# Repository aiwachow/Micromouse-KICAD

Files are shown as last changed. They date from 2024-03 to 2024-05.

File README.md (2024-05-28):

# Micromouse 2.0 class robot 
Micromouse is a autonomous robot whose purpose is to drive through the maze in the shortest time. 
This design include microcontrollers like STM32 and ESP32. Esp was added to testing over-the-air update  
and wireless communication for STM32. Walls are detecting by IR diodes and phototransistors. 

micromousik

## Used software: 
kicadlogo stm32cubeideLOGO
## Things that have been tested and work:
- [x] Hardware 
- [x] STM32, flashing via ST-LINK  
- [x] Dc motors (with driver)
- [x] Encoders 
- [x] Proximity sensor 
- [ ] ESP32

## Software 

In the future, there will be a description of two approaches to the robot's software, as two two-person teams are working on the project.

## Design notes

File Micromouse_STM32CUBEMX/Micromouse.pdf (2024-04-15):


15/04/2024

## Micromouse Project Configuration Report

# 1. Description

## 1.1. Project

Project Name | Micromouse
Board Name | custom
Generated with: | STM32CubeMX 6.8.1
Date | 04/15/2024

## 1.2. MCU

MCU Series | STM32F4
MCU Line | STM32F405/415
MCU name | STM32F405RGTx
MCU Package | LQFP64
MCU Pin number | 64

## 1.3. Core(s) information

Core(s) | Arm Cortex-M4

# 2. Pinout Configuration

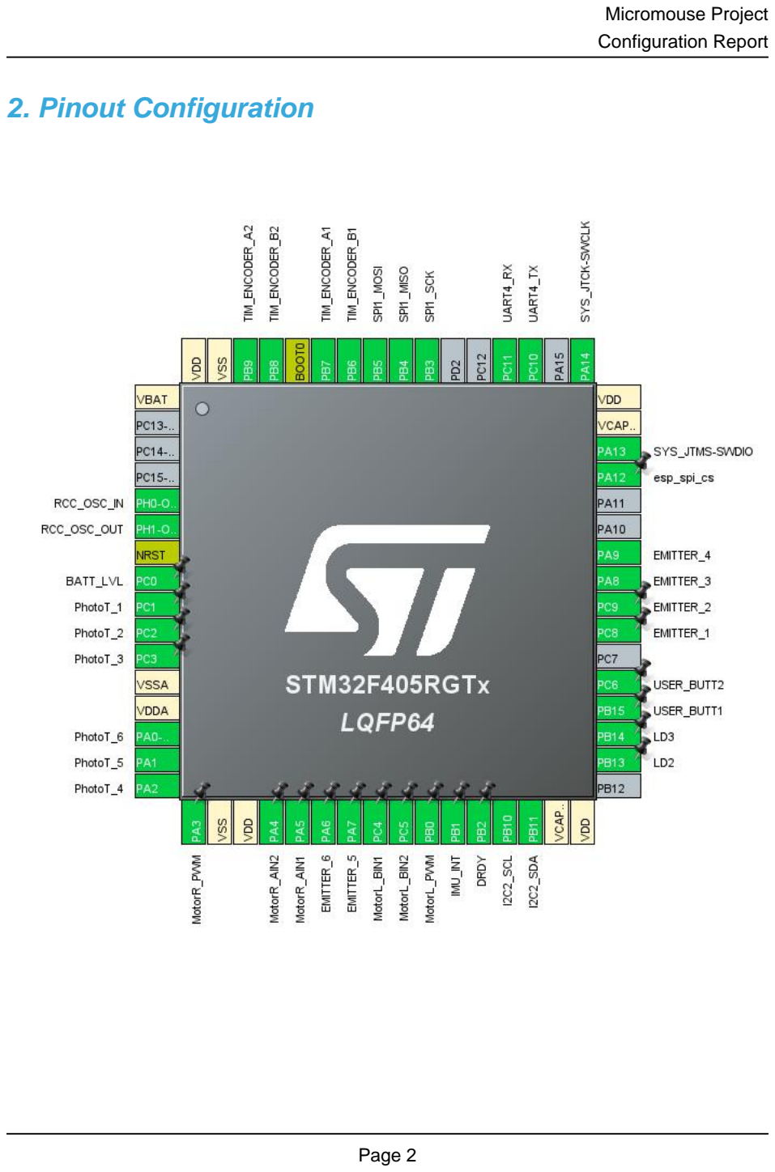
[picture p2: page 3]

# 3. Pins Configuration

Pin Number LQFP64 | Pin Name (function after reset) | Pin Type | Alternate Function(s) | Label
1 | VBAT | Power
5 | PH0-OSC_IN | I/O | RCC_OSC_IN
6 | PH1-OSC_OUT | I/O | RCC_OSC_OUT
7 | NRST | Reset
8 | PC0 | I/O | ADC3_IN10 | BATT_LVL
9 | PC1 | I/O | ADC1_IN11 | PhotoT_1
10 | PC2 | I/O | ADC1_IN12 | PhotoT_2
11 | PC3 | I/O | ADC1_IN13 | PhotoT_3
12 | VSSA | Power
13 | VDDA | Power
14 | PA0-WKUP | I/O | ADC1_IN0 | PhotoT_6
15 | PA1 | I/O | ADC1_IN1 | PhotoT_5
16 | PA2 | I/O | ADC1_IN2 | PhotoT_4
17 | PA3 | I/O | TIM9_CH2 | MotorR_PWM
18 | VSS | Power
19 | VDD | Power
20 | PA4 * | I/O | GPIO_Output | MotorR_AIN2
21 | PA5 * | I/O | GPIO_Output | MotorR_AIN1
22 | PA6 | I/O | TIM3_CH1 | EMITTER_6
23 | PA7 | I/O | TIM3_CH2 | EMITTER_5
24 | PC4 * | I/O | GPIO_Output | MotorL_BIN1
25 | PC5 * | I/O | GPIO_Output | MotorL_BIN2
26 | PB0 | I/O | TIM3_CH3 | MotorL_PWM
27 | PB1 | I/O | GPIO_EXTI1 | IMU_INT
28 | PB2 | I/O | GPIO_EXTI2 | DRDY
29 | PB10 | I/O | I2C2_SCL
30 | PB11 | I/O | I2C2_SDA
31 | VCAP_1 | Power
32 | VDD | Power
34 | PB13 * | I/O | GPIO_Output | LD2
35 | PB14 * | I/O | GPIO_Output | LD3
36 | PB15 | I/O | GPIO_EXTI15 | USER_BUTT1
37 | PC6 | I/O | GPIO_EXTI6 | USER_BUTT2
39 | PC8 | I/O | TIM8_CH3 | EMITTER_1
40 | PC9 | I/O | TIM3_CH4 | EMITTER_2
41 | PA8 | I/O | TIM1_CH1 | EMITTER_3

Pin Number LQFP64 | Pin Name (function after reset) | Pin Type | Alternate Function(s) | Label
42 | PA9 | I/O | TIM1_CH2 | EMITTER_4
45 | PA12 * | I/O | GPIO_Output | esp_spi_cs
46 | PA13 | I/O | SYS_JTMS-SWDIO
47 | VCAP_2 | Power
48 | VDD | Power
49 | PA14 | I/O | SYS_JTCK-SWCLK
51 | PC10 | I/O | UART4_TX
52 | PC11 | I/O | UART4_RX
55 | PB3 | I/O | SPI1_SCK
56 | PB4 | I/O | SPI1_MISO
57 | PB5 | I/O | SPI1_MOSI
58 | PB6 | I/O | TIM4_CH1 | TIM_ENCODER_B1
59 | PB7 | I/O | TIM4_CH2 | TIM_ENCODER_A1
60 | BOOT0 | Boot
61 | PB8 | I/O | TIM4_CH3 | TIM_ENCODER_B2
62 | PB9 | I/O | TIM4_CH4 | TIM_ENCODER_A2
63 | VSS | Power
64 | VDD | Power

## * The pin is affected with an I/O function

# 4. Clock Tree Configuration

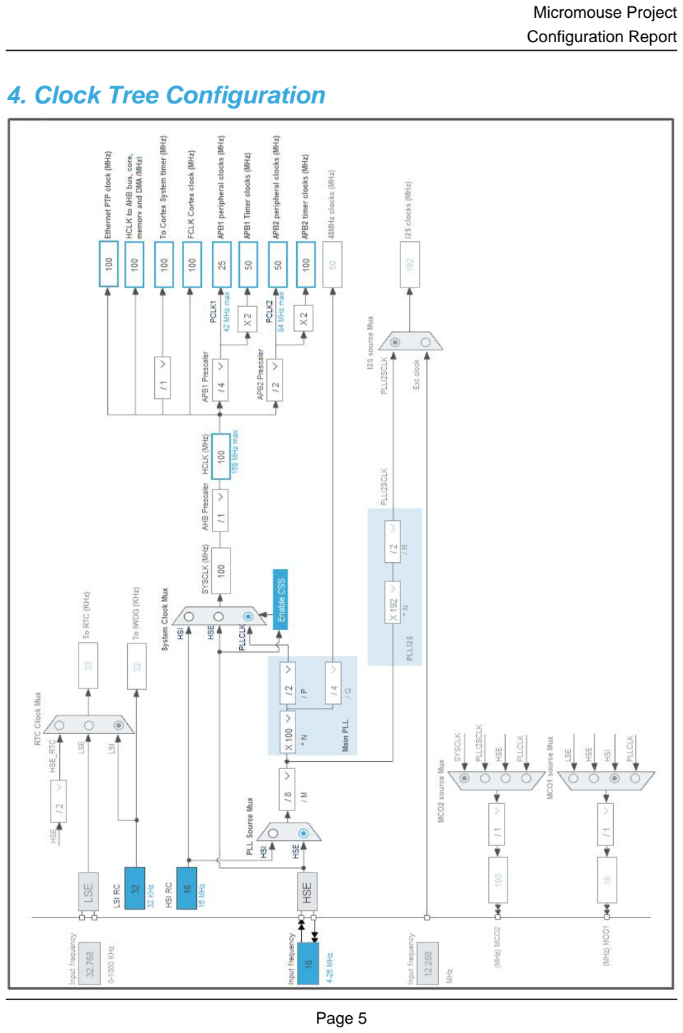
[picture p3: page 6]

# 5. Software Project

## 5.1. Project Settings

Name | Value
Project Name | Micromouse
Project Folder | D:\Micromouse\Micromouse_Kicad\Micromouse_STM32CUBEMX
Toolchain / IDE | STM32CubeIDE
Firmware Package Name and Version | STM32Cube FW_F4 V1.27.1
Application Structure | Advanced
Generate Under Root | Yes
Do not generate the main() | No
Minimum Heap Size | 0x200
Minimum Stack Size | 0x400

## 5.2. Code Generation Settings

Name | Value
STM32Cube MCU packages and embedded software | Copy only the necessary library files
Generate peripheral initialization as a pair of '.c/.h' files | No
Backup previously generated files when re-generating | No
Keep User Code when re-generating | Yes
Delete previously generated files when not re-generated | Yes
Set all free pins as analog (to optimize the power consumption) | No
Enable Full Assert | No

## 5.3. Advanced Settings - Generated Function Calls

Rank | Function Name | Peripheral Instance Name
1 | SystemClock_Config | RCC
2 | MX_GPIO_Init | GPIO
3 | MX_DMA_Init | DMA
4 | MX_ADC1_Init | ADC1
5 | MX_SPI1_Init | SPI1
6 | MX_TIM1_Init | TIM1
7 | MX_TIM3_Init | TIM3
8 | MX_TIM4_Init | TIM4
9 | MX_UART4_Init | UART4
10 | MX_I2C2_Init | I2C2
11 | MX_TIM8_Init | TIM8

Rank | Function Name | Peripheral Instance Name
12 | MX_TIM9_Init | TIM9
13 | MX_ADC3_Init | ADC3

# 6. Power Consumption Calculator report

## 6.1. Microcontroller Selection

Series | STM32F4
Line | STM32F405/415
MCU | STM32F405RGTx
Datasheet | DS8626_Rev8

## 6.2. Parameter Selection

Temperature | 25
Vdd | 3.3

## 6.3. Battery Selection

Battery | Li-SOCL2(A3400)
Capacity | 3400.0 mAh
Self Discharge | 0.08 %/month
Nominal Voltage | 3.6 V
Max Cont Current | 100.0 mA
Max Pulse Current | 200.0 mA
Cells in series | 1
Cells in parallel | 1

## 6.4. Sequence

Step | Step1 | Step2
Mode | RUN | STOP
Vdd | 3.3 | 3.3
Voltage Source | Battery | Battery
Range | Scale1-High | No Scale
Fetch Type | FLASH | n/a
CPU Frequency | 168 MHz | 0 Hz
Clock Configuration | HSE PLL | Regulator_LP Flash-PwrDwn
Clock Source Frequency | 4 MHz | 0 Hz

### Peripherals

Additional Cons. | 0 mA | 0 mA
Average Current | 46 mA | 280 µA
Duration | 0.1 ms | 0.9 ms
DMIPS | 210.0 | 0.0
Ta Max | 98.02 | 104.96
Category | In DS Table | In DS Table

## 6.5. Results

Sequence Time | 1 ms | Average Current | 4.85 mA
Battery Life | 29 days, 4 hours | Average DMIPS | 210.0 DMIPS

## 6.6. Chart

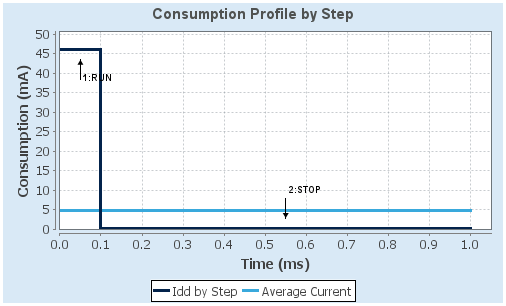
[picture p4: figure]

# 7. Peripherals and Middlewares Configuration

## 7.1. ADC1 mode: IN0 mode: IN1 mode: IN2 mode: IN11 mode: IN12 mode: IN13

## 7.1.1. Parameter Settings:

### ADCs_Common_Settings:

Mode | Independent mode

### ADC_Settings:

Clock Prescaler | PCLK2 divided by 4 *
Resolution | 12 bits (15 ADC Clock cycles)
Data Alignment | Right alignment
Scan Conversion Mode | Enabled
Continuous Conversion Mode | Enabled *
Discontinuous Conversion Mode | Disabled
DMA Continuous Requests | Enabled *
End Of Conversion Selection | EOC flag at the end of single channel conversion

### ADC_Regular_ConversionMode:

Number Of Conversion | 6 *
External Trigger Conversion Source | Regular Conversion launched by software
External Trigger Conversion Edge | None
Rank | 1
Channel | Channel 11 *
Sampling Time | 480 Cycles *
Rank | 2 *
Channel | Channel 12 *
Sampling Time | 480 Cycles *
Rank | 3 *
Channel | Channel 13 *
Sampling Time | 480 Cycles *
Rank | 4 *
Channel | Channel 2 *
Sampling Time | 480 Cycles *

Rank | 5 *
Channel | Channel 1 *
Sampling Time | 480 Cycles *
Rank | 6 *
Channel | Channel 0
Sampling Time | 480 Cycles *

### ADC_Injected_ConversionMode:

Number Of Conversions | 0

### WatchDog:

Enable Analog WatchDog Mode | false

## 7.2. ADC3 mode: IN10

## 7.2.1. Parameter Settings:

### ADC_Settings:

Clock Prescaler | PCLK2 divided by 4 *
Resolution | 12 bits (15 ADC Clock cycles)
Data Alignment | Right alignment
Scan Conversion Mode | Disabled
Continuous Conversion Mode | Enabled *
Discontinuous Conversion Mode | Disabled
DMA Continuous Requests | Disabled
End Of Conversion Selection | EOC flag at the end of single channel conversion

### ADC_Regular_ConversionMode:

Number Of Conversion | 1
External Trigger Conversion Source | Regular Conversion launched by software
External Trigger Conversion Edge | None
Rank | 1
Channel | Channel 10
Sampling Time | 480 Cycles *

### ADC_Injected_ConversionMode:

Number Of Conversions | 0

### WatchDog:

Enable Analog WatchDog Mode | false

## 7.3. I2C2 I2C: I2C

## 7.3.1. Parameter Settings:

### Master Features:

I2C Speed Mode | Fast Mode *
I2C Clock Speed (Hz) | 400000
Fast Mode Duty Cycle | Duty cycle Tlow/Thigh = 2

### Slave Features:

Clock No Stretch Mode | Disabled
Primary Address Length selection | 7-bit
Dual Address Acknowledged | Disabled
Primary slave address | 0
General Call address detection | Disabled

## 7.4. RCC High Speed Clock (HSE): Crystal/Ceramic Resonator

## 7.4.1. Parameter Settings:

### System Parameters:

VDD voltage (V) | 3.3
Instruction Cache | Enabled
Prefetch Buffer | Enabled
Data Cache | Enabled
Flash Latency(WS) | 3 WS (4 CPU cycle)

### RCC Parameters:

HSI Calibration Value | 16
HSE Startup Timout Value (ms) | 100
LSE Startup Timout Value (ms) | 5000

### Power Parameters:

Power Regulator Voltage Scale | Power Regulator Voltage Scale 1

## 7.5. SPI1 Mode: Full-Duplex Master

## 7.5.1. Parameter Settings:

### Basic Parameters:

Frame Format | Motorola
Data Size | 8 Bits
First Bit | MSB First

### Clock Parameters:

Prescaler (for Baud Rate) | 8 *
Baud Rate | 6.25 MBits/s *
Clock Polarity (CPOL) | Low
Clock Phase (CPHA) | 1 Edge

### Advanced Parameters:

CRC Calculation | Disabled
NSS Signal Type | Software

## 7.6. SYS Debug: Serial Wire

## 7.7. TIM1 Clock Source : Internal Clock Channel1: PWM Generation CH1 Channel2: PWM Generation CH2

## 7.7.1. Parameter Settings:

### Counter Settings:

Prescaler (PSC - 16 bits value) | 19 *
Counter Mode | Up
Counter Period (AutoReload Register - 16 bits value ) | 99 *
Internal Clock Division (CKD) | No Division
Repetition Counter (RCR - 8 bits value) | 0
auto-reload preload | Disable

### Trigger Output (TRGO) Parameters:

Master/Slave Mode (MSM bit) | Disable (Trigger input effect not delayed)
Trigger Event Selection | Reset (UG bit from TIMx_EGR)

### Break And Dead Time management - BRK Configuration:

BRK State | Disable
BRK Polarity | High

### Break And Dead Time management - Output Configuration:

Automatic Output State | Disable
Off State Selection for Run Mode (OSSR) | Disable
Off State Selection for Idle Mode (OSSI) | Disable
Lock Configuration | Off

### PWM Generation Channel 1:

Mode | PWM mode 1
Pulse (16 bits value) | 0
Output compare preload | Enable
Fast Mode | Disable
CH Polarity | High
CH Idle State | Reset

### PWM Generation Channel 2:

Mode | PWM mode 1
Pulse (16 bits value) | 0
Output compare preload | Enable
Fast Mode | Disable
CH Polarity | High
CH Idle State | Reset

## 7.8. TIM3 Clock Source : Internal Clock Channel1: PWM Generation CH1 Channel2: PWM Generation CH2 Channel3: PWM Generation CH3 Channel4: PWM Generation CH4

## 7.8.1. Parameter Settings:

### Counter Settings:

Prescaler (PSC - 16 bits value) | 9 *
Counter Mode | Up
Counter Period (AutoReload Register - 16 bits value ) | 99 *
Internal Clock Division (CKD) | No Division
auto-reload preload | Disable

### Trigger Output (TRGO) Parameters:

Master/Slave Mode (MSM bit) | Disable (Trigger input effect not delayed)
Trigger Event Selection | Reset (UG bit from TIMx_EGR)

### PWM Generation Channel 1:

Mode | PWM mode 1
Pulse (16 bits value) | 0
Output compare preload | Enable
Fast Mode | Disable
CH Polarity | High

### PWM Generation Channel 2:

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

### PWM Generation Channel 3:

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

### PWM Generation Channel 4:

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

## 7.9. TIM4 Channel1: Input Capture direct mode Channel2: Input Capture direct mode Channel3: Input Capture direct mode Channel4: Input Capture direct mode

## 7.9.1. Parameter Settings:

### Counter Settings:

Prescaler (PSC - 16 bits value) | 0
Counter Mode | Up
Counter Period (AutoReload Register - 16 bits value ) | 65535
Internal Clock Division (CKD) | No Division
auto-reload preload | Disable

### Trigger Output (TRGO) Parameters:

Master/Slave Mode (MSM bit) | Disable (Trigger input effect not delayed)

Trigger Event Selection | Reset (UG bit from TIMx_EGR)

### Input Capture Channel 1:

Polarity Selection | Rising Edge
IC Selection | Direct
Prescaler Division Ratio | No division
Input Filter (4 bits value) | 0

### Input Capture Channel 2:

Polarity Selection | Rising Edge
IC Selection | Direct
Prescaler Division Ratio | No division
Input Filter (4 bits value) | 0

### Input Capture Channel 3:

Polarity Selection | Rising Edge
IC Selection | Direct
Prescaler Division Ratio | No division
Input Filter (4 bits value) | 0

### Input Capture Channel 4:

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

## 7.10. TIM8 Clock Source : Internal Clock Channel3: PWM Generation CH3

## 7.10.1. Parameter Settings:

### Counter Settings:

Prescaler (PSC - 16 bits value) | 19 *
Counter Mode | Up
Counter Period (AutoReload Register - 16 bits value ) | 99 *
Internal Clock Division (CKD) | No Division
Repetition Counter (RCR - 8 bits value) | 0
auto-reload preload | Disable

### Trigger Output (TRGO) Parameters:

Master/Slave Mode (MSM bit) | Disable (Trigger input effect not delayed)
Trigger Event Selection | Reset (UG bit from TIMx_EGR)

### Break And Dead Time management - BRK Configuration:

BRK State | Disable

BRK Polarity | High

### Break And Dead Time management - Output Configuration:

Automatic Output State | Disable
Off State Selection for Run Mode (OSSR) | Disable
Off State Selection for Idle Mode (OSSI) | Disable
Lock Configuration | Off

### PWM Generation Channel 3:

Mode | PWM mode 1
Pulse (16 bits value) | 0
Output compare preload | Enable
Fast Mode | Disable
CH Polarity | High
CH Idle State | Reset

## 7.11. TIM9 mode: Clock Source Channel2: PWM Generation CH2

## 7.11.1. Parameter Settings:

### Counter Settings:

Prescaler (PSC - 16 bits value) | 19 *
Counter Mode | Up
Counter Period (AutoReload Register - 16 bits value ) | 99 *
Internal Clock Division (CKD) | No Division
auto-reload preload | Disable

### PWM Generation Channel 2:

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

## 7.12. UART4 Mode: Asynchronous

## 7.12.1. Parameter Settings:

### Basic Parameters:

Baud Rate | 115200
Word Length | 8 Bits (including Parity)
Parity | None
Stop Bits | 1

### Advanced Parameters:

Data Direction | Receive and Transmit
Over Sampling | 16 Samples

### * User modified value

# 8. System Configuration

## 8.1. GPIO configuration

IP | Pin | Signal | GPIO mode | GPIO pull/up pull down

## Max Speed

## User Label

ADC1 | PC1 | ADC1_IN11 | Analog mode | No pull-up and no pull-down | n/a | PhotoT_1
| PC2 | ADC1_IN12 | Analog mode | No pull-up and no pull-down | n/a | PhotoT_2
| PC3 | ADC1_IN13 | Analog mode | No pull-up and no pull-down | n/a | PhotoT_3
| PA0-WKUP | ADC1_IN0 | Analog mode | No pull-up and no pull-down | n/a | PhotoT_6
| PA1 | ADC1_IN1 | Analog mode | No pull-up and no pull-down | n/a | PhotoT_5
| PA2 | ADC1_IN2 | Analog mode | No pull-up and no pull-down | n/a | PhotoT_4
ADC3 | PC0 | ADC3_IN10 | Analog mode | No pull-up and no pull-down | n/a | BATT_LVL
I2C2 | PB10 | I2C2_SCL | Alternate Function Open Drain | No pull-up and no pull-down | Very High
*
| PB11 | I2C2_SDA | Alternate Function Open Drain | No pull-up and no pull-down | Very High
*
RCC | PH0- OSC_IN | RCC_OSC_IN | n/a | n/a | n/a
| PH1- OSC_OUT | RCC_OSC_OUT | n/a | n/a | n/a
SPI1 | PB3 | SPI1_SCK | Alternate Function Push Pull | No pull-up and no pull-down | Very High
*
| PB4 | SPI1_MISO | Alternate Function Push Pull | No pull-up and no pull-down | Very High
*
| PB5 | SPI1_MOSI | Alternate Function Push Pull | No pull-up and no pull-down | Very High
*
SYS | PA13 | SYS_JTMS- SWDIO | n/a | n/a | n/a
| PA14 | SYS_JTCK- SWCLK | n/a | n/a | n/a
TIM1 | PA8 | TIM1_CH1 | Alternate Function Push Pull | No pull-up and no pull-down | Low | EMITTER_3
| PA9 | TIM1_CH2 | Alternate Function Push Pull | No pull-up and no pull-down | Low | EMITTER_4
TIM3 | PA6 | TIM3_CH1 | Alternate Function Push Pull | No pull-up and no pull-down | Low | EMITTER_6
| PA7 | TIM3_CH2 | Alternate Function Push Pull | No pull-up and no pull-down | Low | EMITTER_5
| PB0 | TIM3_CH3 | Alternate Function Push Pull | No pull-up and no pull-down | Low | MotorL_PWM
| PC9 | TIM3_CH4 | Alternate Function Push Pull | No pull-up and no pull-down | Low | EMITTER_2
TIM4 | PB6 | TIM4_CH1 | Alternate Function Push Pull | No pull-up and no pull-down | Low | TIM_ENCODER_B1
| PB7 | TIM4_CH2 | Alternate Function Push Pull | No pull-up and no pull-down | Low | TIM_ENCODER_A1
| PB8 | TIM4_CH3 | Alternate Function Push Pull | No pull-up and no pull-down | Low | TIM_ENCODER_B2
| PB9 | TIM4_CH4 | Alternate Function Push Pull | No pull-up and no pull-down | Low | TIM_ENCODER_A2
TIM8 | PC8 | TIM8_CH3 | Alternate Function Push Pull | No pull-up and no pull-down | Low | EMITTER_1

IP | Pin | Signal | GPIO mode | GPIO pull/up pull down | Max Speed | User Label
TIM9 | PA3 | TIM9_CH2 | Alternate Function Push Pull | No pull-up and no pull-down | Low | MotorR_PWM
UART4 | PC10 | UART4_TX | Alternate Function Push Pull | No pull-up and no pull-down | Very High *
| PC11 | UART4_RX | Alternate Function Push Pull | No pull-up and no pull-down | Very High *
GPIO | PA4 | GPIO_Output | Output Push Pull | No pull-up and no pull-down | Low | MotorR_AIN2
| PA5 | GPIO_Output | Output Push Pull | No pull-up and no pull-down | Low | MotorR_AIN1
| PC4 | GPIO_Output | Output Push Pull | No pull-up and no pull-down | Low | MotorL_BIN1
| PC5 | GPIO_Output | Output Push Pull | No pull-up and no pull-down | Low | MotorL_BIN2
| PB1 | GPIO_EXTI1 | External Interrupt Mode with Rising edge trigger detection | No pull-up and no pull-down | n/a | IMU_INT
| PB2 | GPIO_EXTI2 | External Interrupt Mode with Rising edge trigger detection | No pull-up and no pull-down | n/a | DRDY
| PB13 | GPIO_Output | Output Push Pull | No pull-up and no pull-down | Low | LD2
| PB14 | GPIO_Output | Output Push Pull | No pull-up and no pull-down | Low | LD3
| PB15 | GPIO_EXTI15 | External Interrupt Mode with Rising edge trigger detection | Pull-up * | n/a | USER_BUTT1
| PC6 | GPIO_EXTI6 | External Interrupt Mode with Rising edge trigger detection | Pull-up * | n/a | USER_BUTT2
| PA12 | GPIO_Output | Output Push Pull | No pull-up and no pull-down | Low | esp_spi_cs

## 8.2. DMA configuration

DMA request | Stream | Direction | Priority
ADC1 | DMA2_Stream0 | Peripheral To Memory | High *

## ADC1: DMA2_Stream0 DMA request Settings:

Mode: | Circular *
Use fifo: | Disable
Peripheral Increment: | Disable
Memory Increment: | Enable *
Peripheral Data Width: | Half Word
Memory Data Width: | Half Word

## 8.3. NVIC configuration

## 8.3.1. NVIC

Interrupt Table | Enable | Preenmption Priority | SubPriority
Non maskable interrupt | true | 0 | 0
Hard fault interrupt | true | 0 | 0
Memory management fault | true | 0 | 0
Pre-fetch fault, memory access fault | true | 0 | 0
Undefined instruction or illegal state | true | 0 | 0
System service call via SWI instruction | true | 0 | 0
Debug monitor | true | 0 | 0
Pendable request for system service | true | 0 | 0
System tick timer | true | 15 | 0
DMA2 stream0 global interrupt | true | 0 | 0
PVD interrupt through EXTI line 16 | unused
Flash global interrupt | unused
RCC global interrupt | unused
EXTI line1 interrupt | unused
EXTI line2 interrupt | unused
ADC1, ADC2 and ADC3 global interrupts | unused
EXTI line[9:5] interrupts | unused
TIM1 break interrupt and TIM9 global interrupt | unused
TIM1 update interrupt and TIM10 global interrupt | unused
TIM1 trigger and commutation interrupts and TIM11 global interrupt | unused
TIM1 capture compare interrupt | unused
TIM3 global interrupt | unused
TIM4 global interrupt | unused
I2C2 event interrupt | unused
I2C2 error interrupt | unused
SPI1 global interrupt | unused
EXTI line[15:10] interrupts | unused
TIM8 break interrupt and TIM12 global interrupt | unused
TIM8 update interrupt and TIM13 global interrupt | unused
TIM8 trigger and commutation interrupts and TIM14 global interrupt | unused
TIM8 capture compare interrupt | unused
UART4 global interrupt | unused
FPU global interrupt | unused

## 8.3.2. NVIC Code generation

Enabled interrupt Table | Select for init sequence ordering | Generate IRQ handler | Call HAL handler
Non maskable interrupt | false | true | false
Hard fault interrupt | false | true | false
Memory management fault | false | true | false
Pre-fetch fault, memory access fault | false | true | false
Undefined instruction or illegal state | false | true | false
System service call via SWI instruction | false | true | false
Debug monitor | false | true | false
Pendable request for system service | false | true | false
System tick timer | false | true | true
DMA2 stream0 global interrupt | false | true | true

### * User modified value

# 9. System Views

## 9.1. Category view 9.1.1. Current

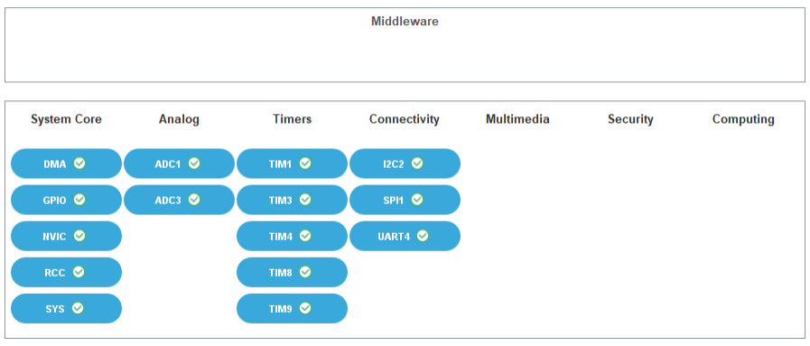
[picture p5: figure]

# 10. Docs & Resources

Type | Link

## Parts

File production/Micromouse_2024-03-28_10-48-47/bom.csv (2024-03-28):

Designator | Footprint | Quantity | Value | LCSC Part #
C201, C304, C306, C307, C309, C310, C312, C314, C315, C316, C317, C318, C319, C320, C321, C323, C324, C401, C404, C405, C406 | 0402 | 21 | 100n | C307331
C202, C403, C407, C501, C502, C503, C504, C505, C506 | 0603 | 9 | 100n | C14663
C203, C207 | 0603 | 2 | 1u | C15849
C204 | 0402 | 1 | 4u7 | C23733
C205, C402 | CP_EIA-3216-10_Kemet-I_Pad1.58x1.35mm_HandSolder | 2 | 10u | C7171
C206 | 0402 | 1 | 10n | C15195
C208 | 0603 | 1 | 4u7 | C19666
C301, C303 | 0402 | 2 | 1u | C15849
C302, C305 | 0402 | 2 | 10p | C32949
C308 | 0402 | 1 | 4u7 | C96446
C311, C313 | 0402 | 2 | 2u2 | C12530
C322 | 0805 | 1 | 10u | C307331
D201, D202, D203 | D_SOD-123FL | 3 | D_Schottky
D204 | 0805 | 1 | BATT_LED | C2297
D205 | 0805 | 1 | 3V3_LED | C2297
D302, D303, D305, D306, D307 | 0603 | 5 | LED_WHITE | C2290
D304 | D_SOD-323 | 1 | D_Schottky | C191023
D501, D507, D509 | PinHeader_1x02_P2.54mm_Vertical | 3 | SFH 4550
D502, D503, D504, D505, D506, D508 | PinHeader_1x02_P2.54mm_Vertical | 6 | LED
FB301 | 0603 | 1 | Optionally | C1002
H201, H202, H203, H204 | MountingHole_3mm | 4 | MountingHole
H401, H402, H403, H404 | MountingHole_5mm | 4 | MountingHole
IC302 | ESP32S3MINI1N8 | 1 | ESP32-S3-MINI-1-N8
IC501 | SOIC127P600X175-16N | 1 | ULN2003ADR
J201 | AMASS_XT30U-M_1x02_P5.0mm_Vertical | 1 | XT30
J202 | USB_C_Receptacle_GCT_USB4105-xx-A_16P_TopMnt_Horizontal | 1 | USB_C_Receptacle_USB2.0
J301 | PinHeader_2x05_P2.54mm_Vertical | 1 | Conn_02x05_Counter_Clockwise
J302 | PinHeader_1x04_P2.54mm_Vertical | 1 | Conn_01x04
J401, J402 | PinHeader_1x06_P2.54mm_Vertical | 2 | Conn_01x06
J601 | PinHeader_1x08_P2.54mm_Vertical | 1 | Conn_01x08
J602 | PinHeader_1x05_P2.54mm_Vertical | 1 | Conn_01x05
JP201 | PinHeader_1x02_P2.54mm_Vertical | 1 | Jumper_2_Bridged
Q201 | SOT-23-3 | 1 | PMOS | C15127
Q501 | PinHeader_1x02_P2.54mm_Vertical | 1 | SFH 300 FA-3/4
Q502, Q503, Q504, Q505, Q506 | PinHeader_1x02_P2.54mm_Vertical | 5 | Q_Photo_NPN
R201, R202 | 0402 | 2 | 5k1 | C25905
R203 | 0603 | 1 | 10k | C25804
R204 | 0603 | 1 | 0 | C21189
R205 | 0603 | 1 | 82k | C23254
R206 | 0603 | 1 | 51k | C23196
R207 | 0603 | 1 | 2k2 | C4190
R208, R302, R305, R309, R310, R318, R501, R503, R505, R507, R509, R511, R513, R514, R515 | 0603 | 15 | 1K | C21190
R301 | 0603 | 1 | 1k
R303 | 0402 | 1 | 22 | C25092
R304, R311, R401 | 0402 | 3 | 10k | C25744
R306 | 0603 | 1 | 10k | C25744
R307, R308 | 0402 | 2 | 1k | C11702
R312, R313 | 0603 | 2 | 100
R314, R315, R316 | 0603 | 3 | 22
R317 | 0603 | 1 | 22
R319 | 0603 | 1 | 0
R502, R504, R506, R508, R510, R512 | 0805 | 6 | 47 | C17714
SW201 | SW_Slide_1P2T_CK_OS102011MS2Q | 1 | SW_SPDT
SW301 | SW_PUSH_1P1T_6x3.5mm_H4.3_APEM_MJTP1243 | 1 | NRST
SW302 | SW_E-Switch_EG1271_SPDT | 1 | SW_SPDT
SW303, SW304 | SW_Push_1P1T_NO_6x6mm_H9.5mm | 2 | USER
SW305 | SW_PUSH_1P1T_6x3.5mm_H4.3_APEM_MJTP1243 | 1 | ESP_RST
SW306 | SW_Push_1P1T_NO_6x6mm_H9.5mm | 1 | BOOT
TP202, TP203, TP204, TP205, TP206, TP301 | TestPoint_Pad_D1.0mm | 6 | TestPoint
U201 | SOT-23-6 | 1 | USBLC6-2SC6
U202 | SOT-223-3_TabPin2 | 1 | LDL1117S33R
U301 | LQFP-64_10x10mm_P0.5mm | 1 | STM32F405RGT6 | C15742
U401 | SSOP-24_5.3x8.2mm_P0.65mm | 1 | TB6612FNG
Y301 | Crystal_SMD_3225-4Pin_3.2x2.5mm | 1 | 16MHz|9p|10ppm | C13738

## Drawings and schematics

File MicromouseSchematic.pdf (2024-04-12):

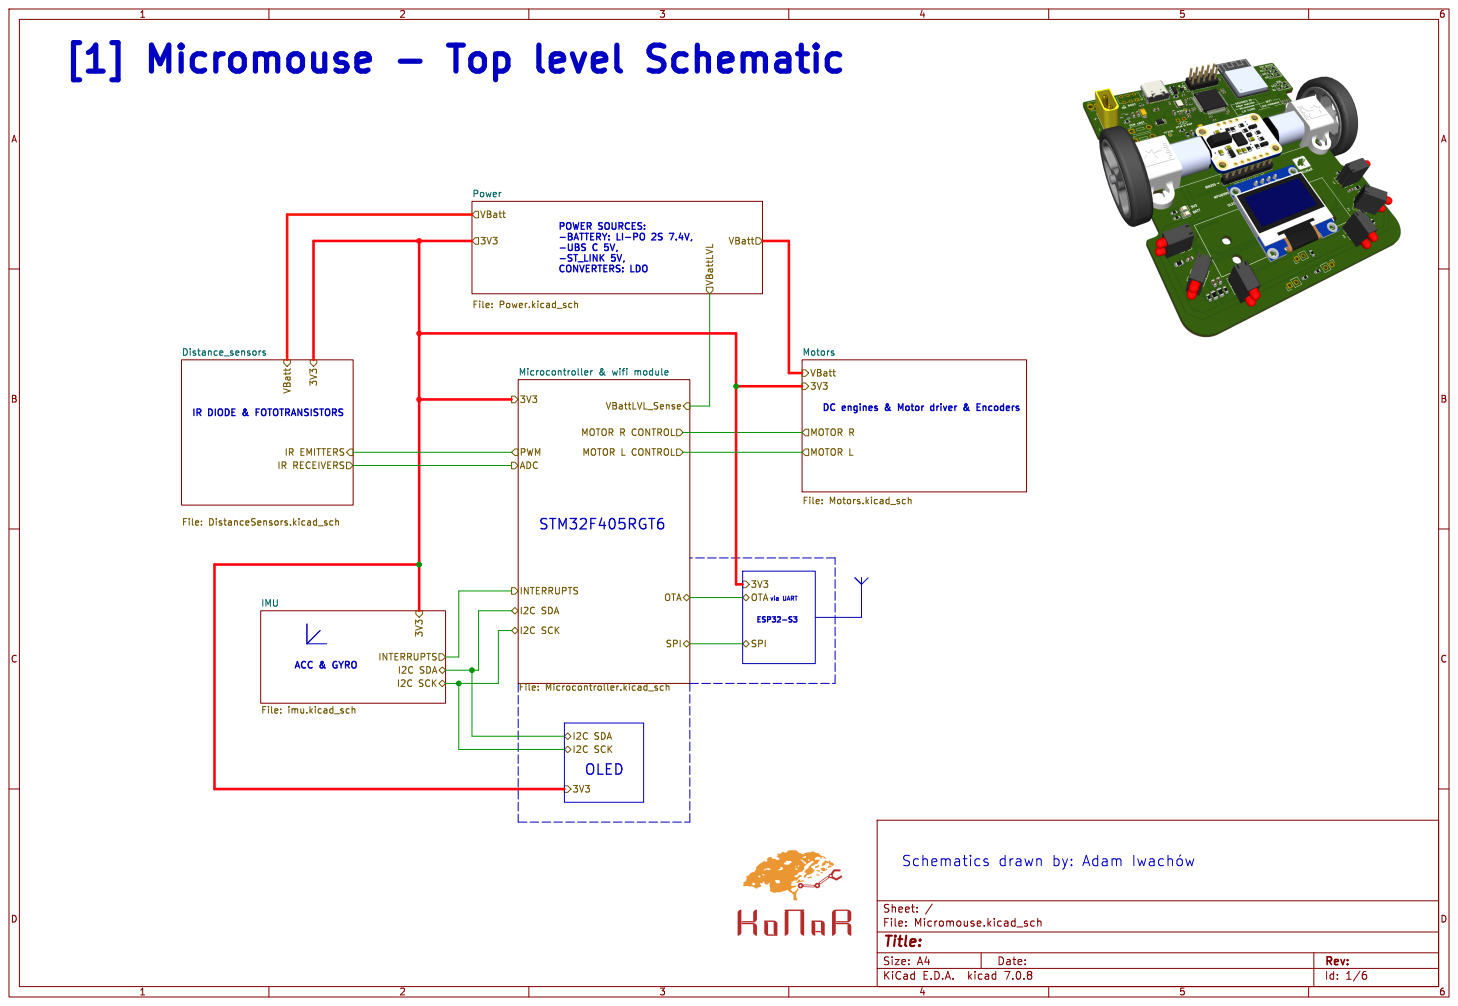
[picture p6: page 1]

Power File: Power.kicad_sch Distance_sensors File: DistanceSensors.kicad_sch

Id: 1/6 Title: File: Micromouse.kicad_sch Sheet: /

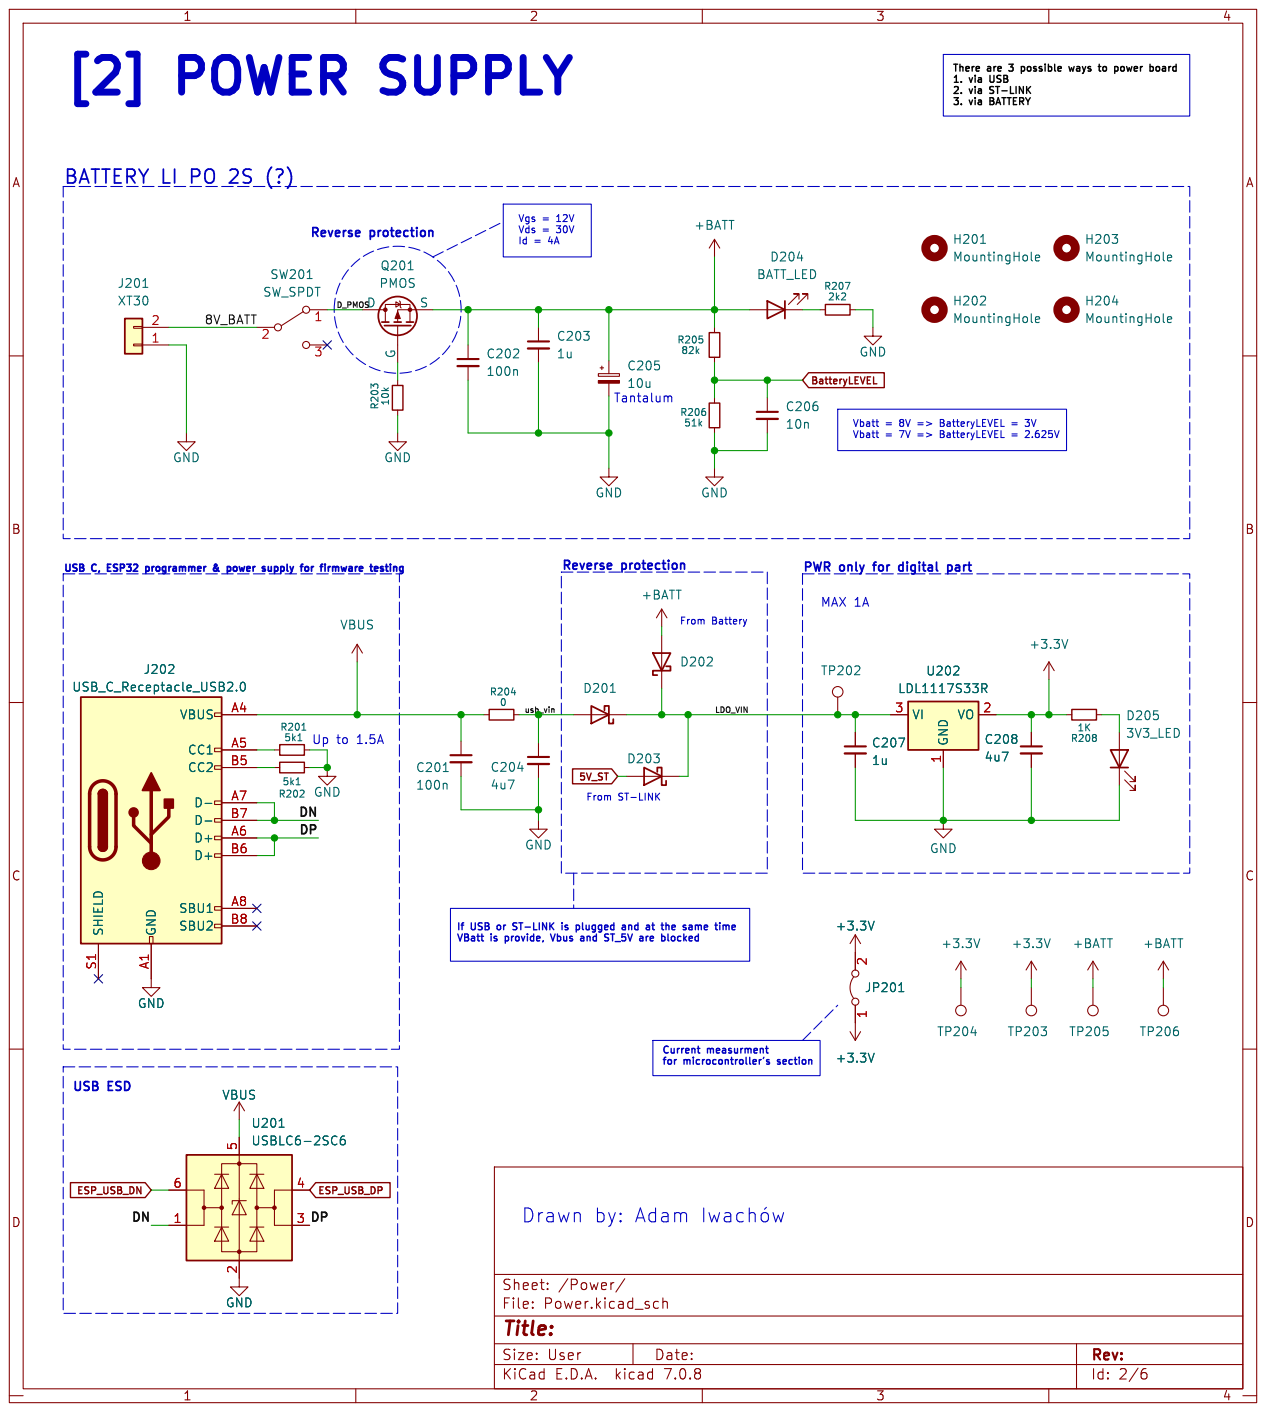
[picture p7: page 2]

There are 3 possible ways to power board
1. via USB
2. via ST-LINK

Id = 4A Reverse protection USB ESD
D_PMOS DPDN

Id: 2/6 Title: File: Power.kicad_sch Sheet: /Power/

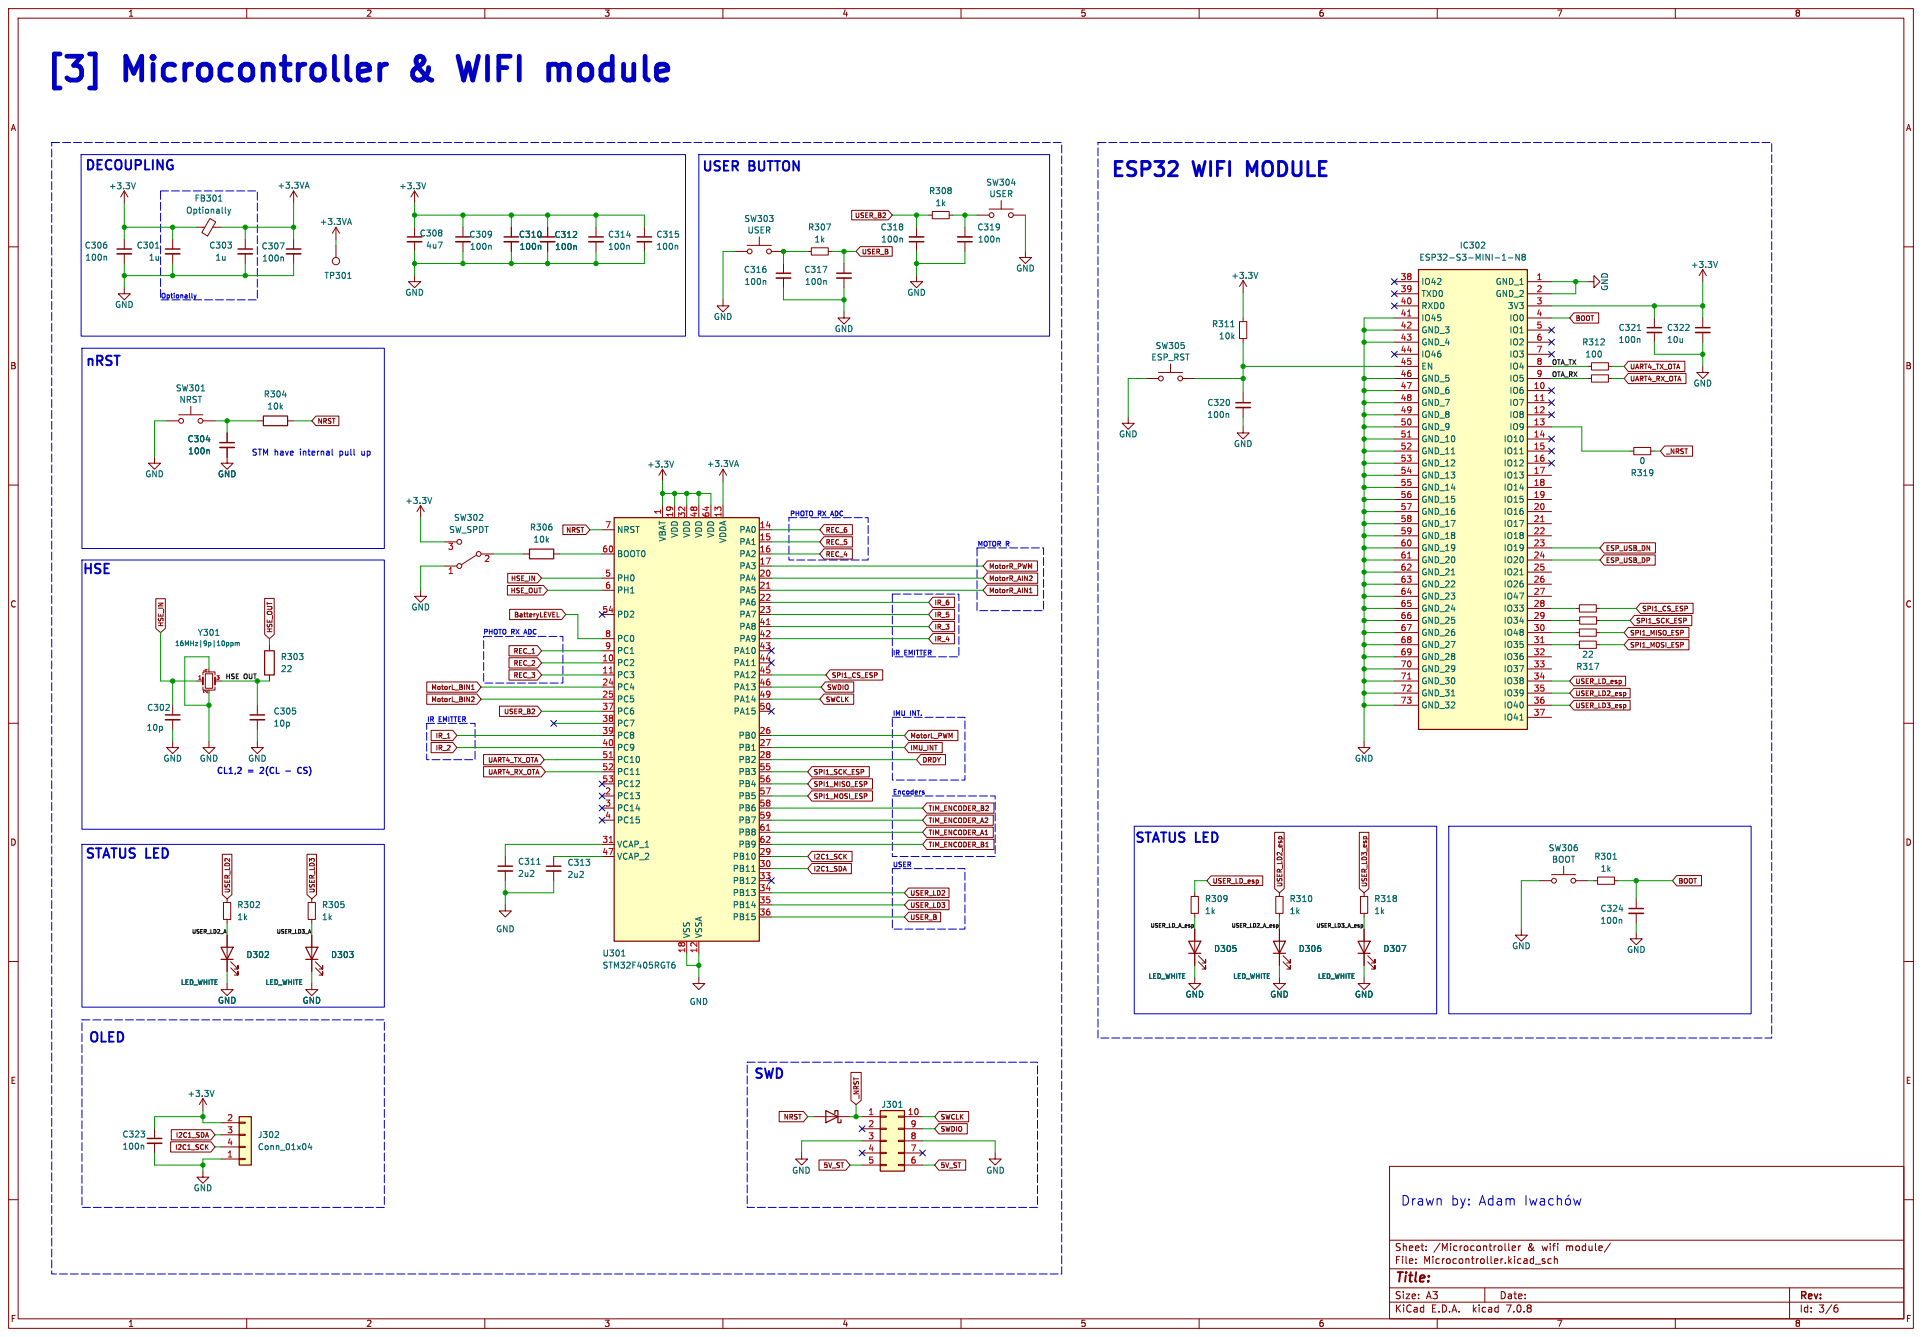
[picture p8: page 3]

1 PC2 10 PC3 11 VSSA 12 VDDA 13 PA0 14 PA1 15 PA2 16 PA3 17 VSS 18 VDD 19 PC13 2 PA4 20 PA5 21 PA6 22 PA7 23 PC4 24 PC5 25 PB0 26 PB1 27 PB2 28 PB10 29 PC14 3 PB11 30 VCAP_1 31 VDD 32 PB12 33 PB13 34 PB14 35 PB15 36 PC6 37 PC7 38 PC8 39 PC15 4 PC9 40 PA8 41 PA9 42 PA10 43 PA11 44 PA12 45 PA13 46 VCAP_2 47 VDD 48 PA14 49 PH0 5 PA15 50 PC10 51 PC11 52 PC12 53 PD2 54 PB3 55 PB4 56 PB5 57 PB6 58 PB7 59 PH1 6 BOOT0 60 PB8 61 PB9 62 VDD 64 NRST 7 PC0 8 PC1 9U301 STM32F405RGT6 C313

PHOTO RX ADC HSE

IMU INT. STATUS LED

Drawn by: Adam þÿIwachów

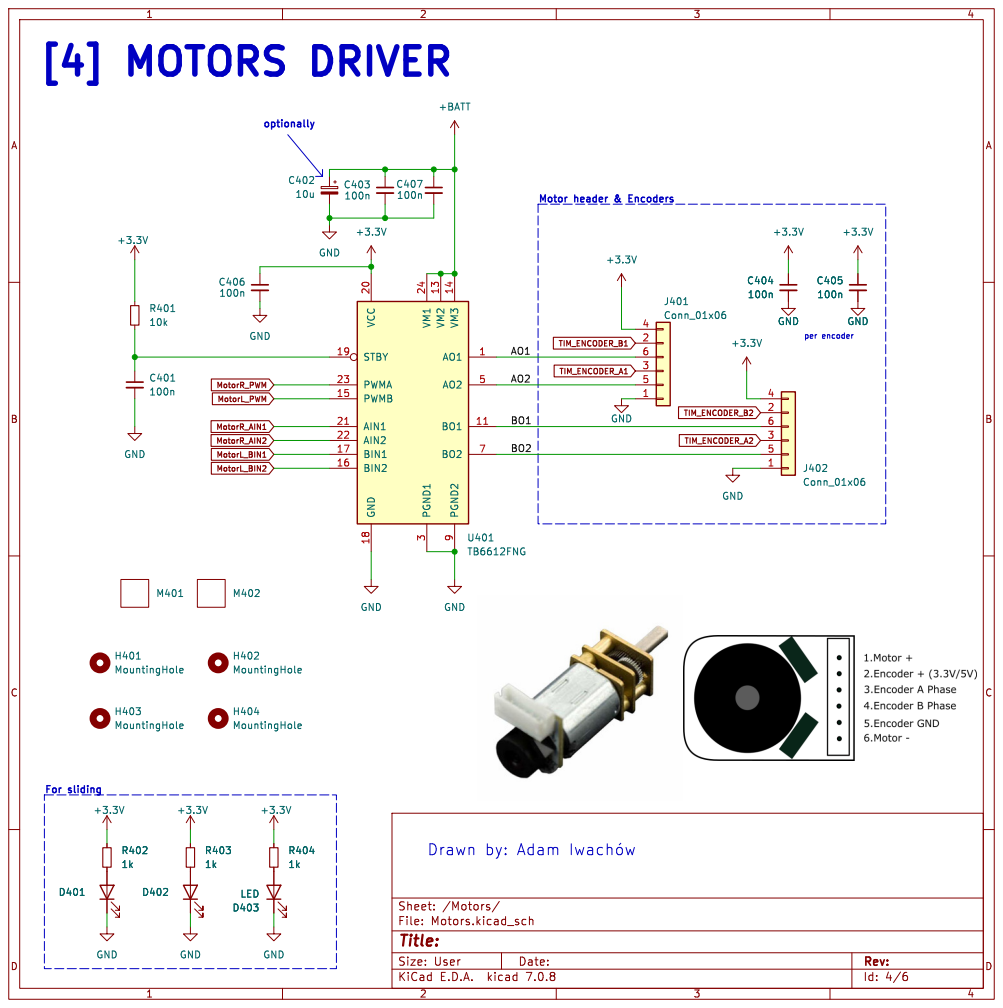
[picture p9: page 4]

Id: 4/6 Title: File: Motors.kicad_sch Sheet: /Motors/

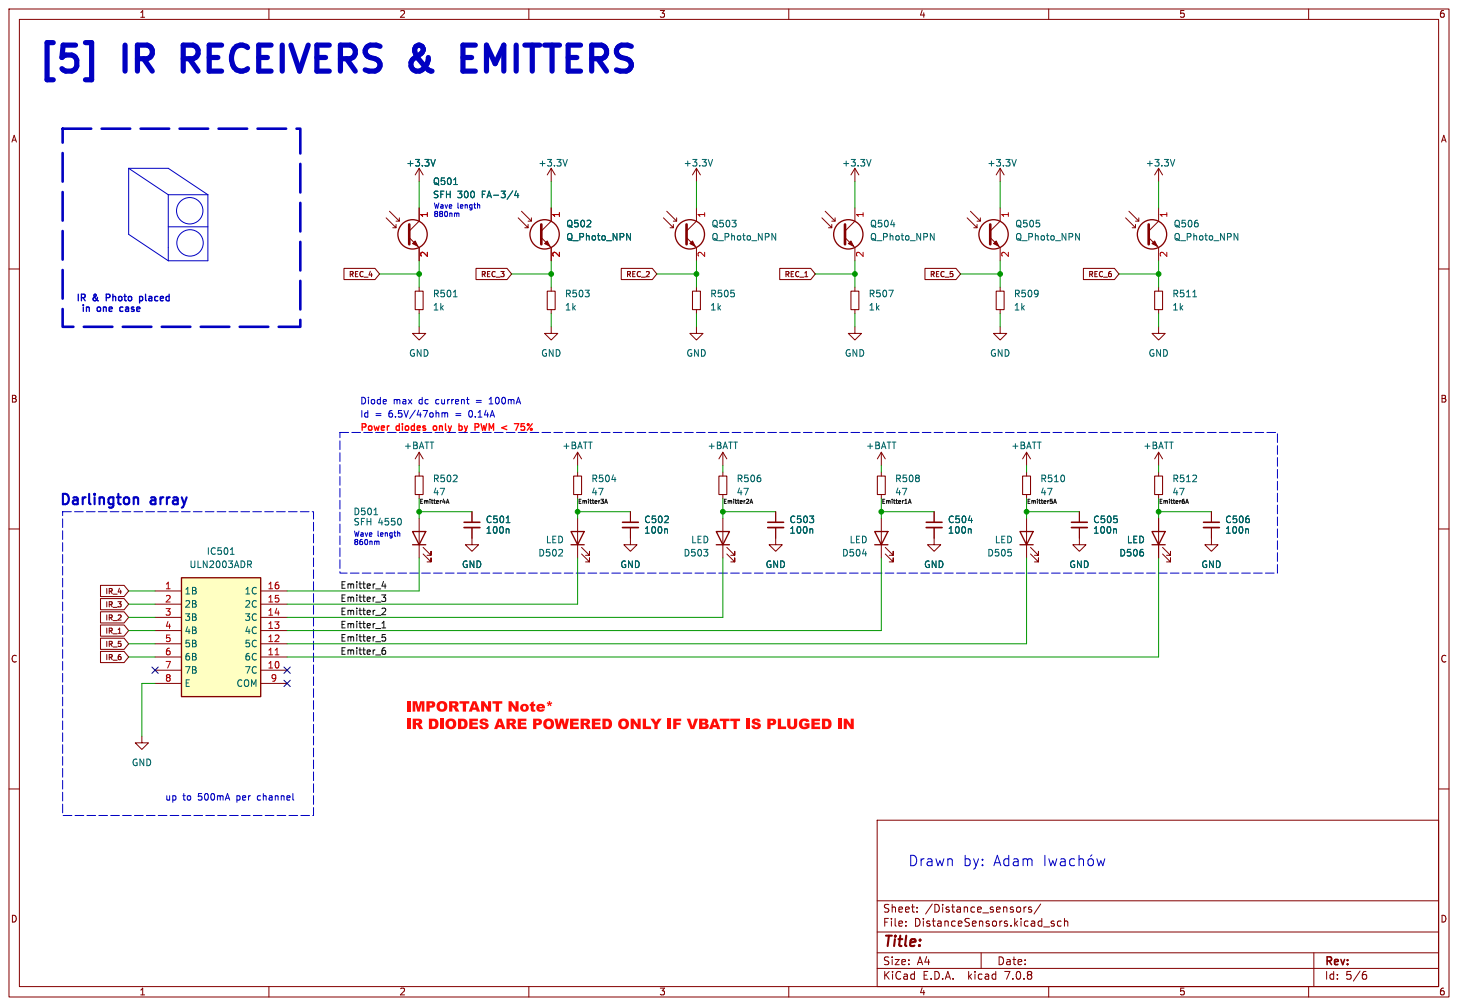
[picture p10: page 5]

in one case Darlington array

Diode max dc current = 100mA

Id: 5/6 Title: File: DistanceSensors.kicad_sch Sheet: /Distance_sensors/ C503
LED GND

IMPORTANT Note*
IR DIODES ARE POWERED ONLY IF VBATT IS PLUGED IN

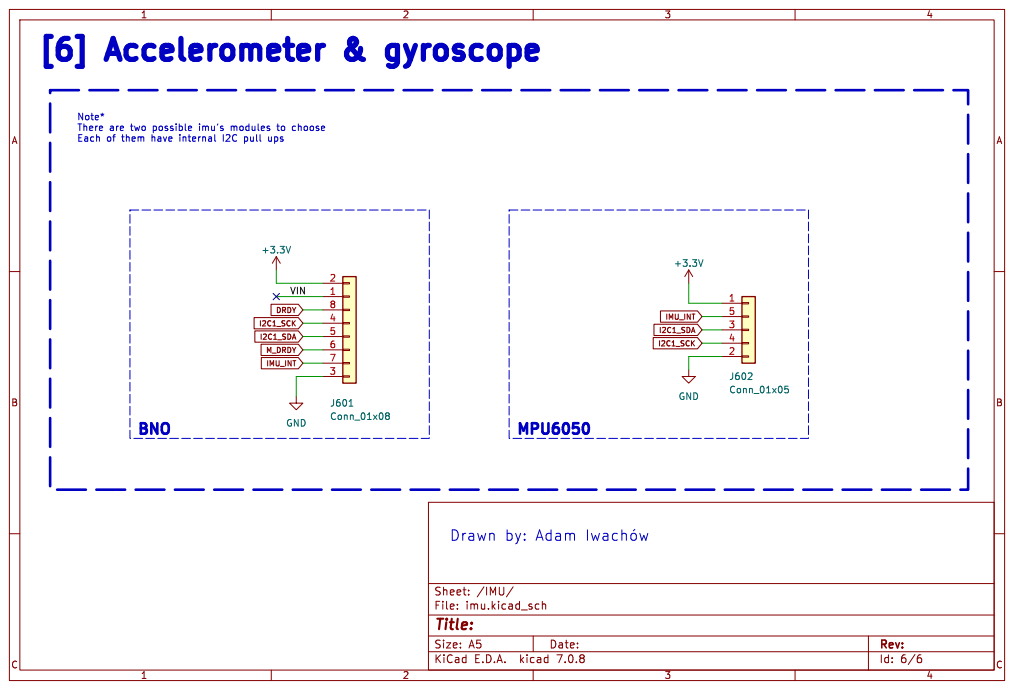
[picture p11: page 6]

Id: 6/6 Title: File: imu.kicad_sch Sheet: /IMU/ +3.3VGND

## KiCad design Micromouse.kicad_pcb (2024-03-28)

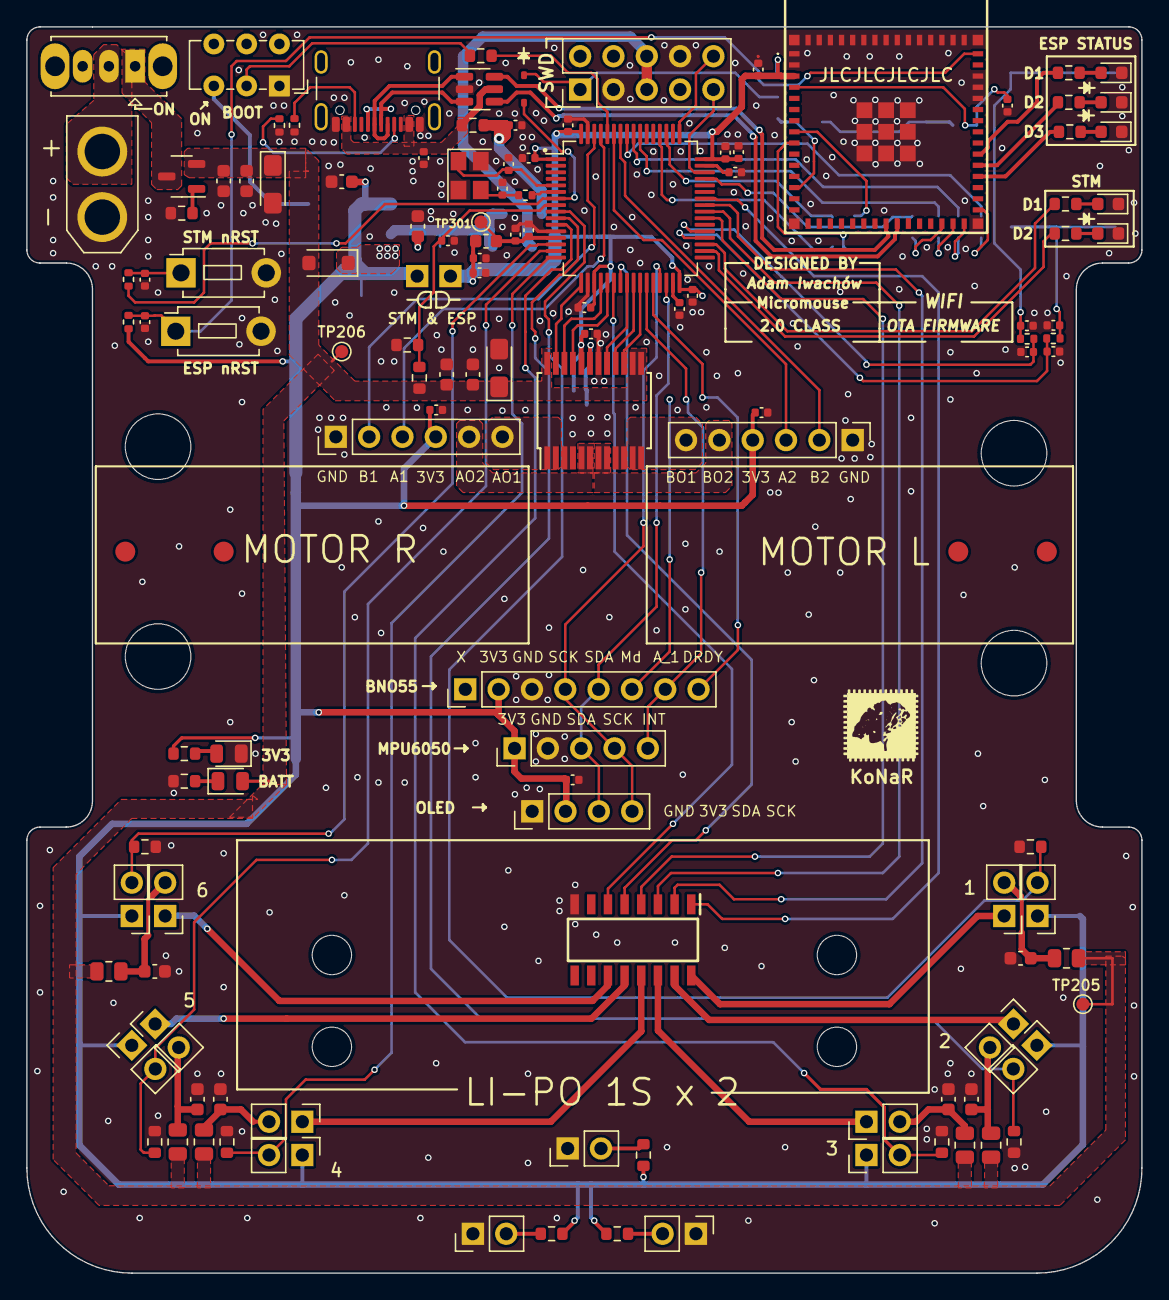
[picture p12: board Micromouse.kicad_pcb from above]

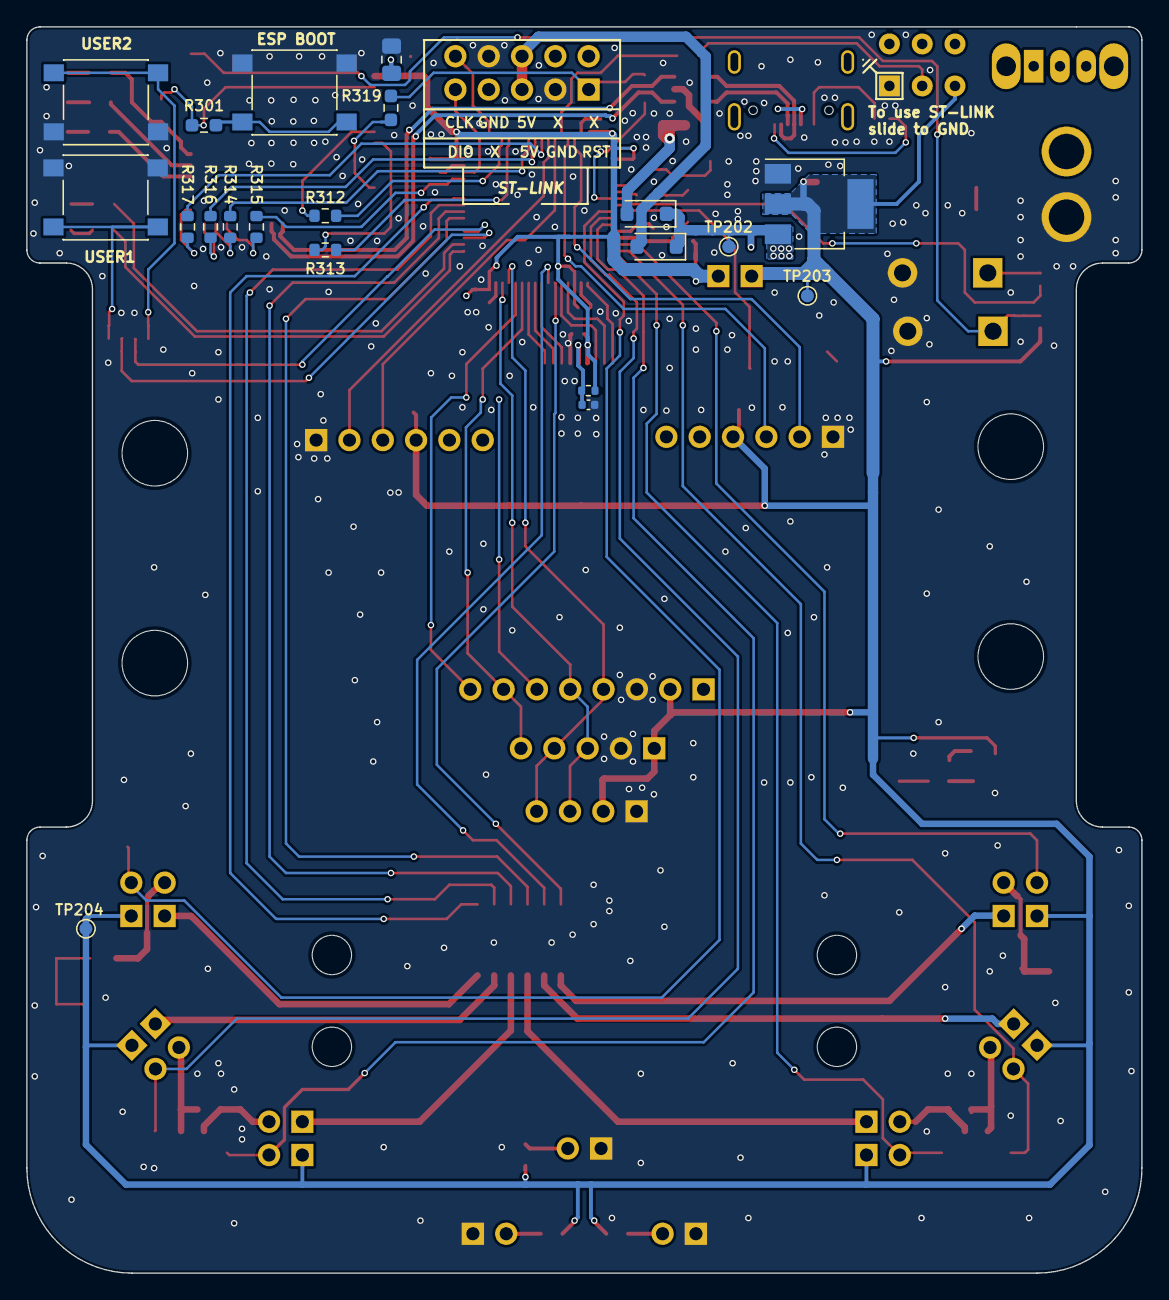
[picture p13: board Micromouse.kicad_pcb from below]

Board: 2 copper layers, 85.0 x 95.0 mm, 153 parts (20 on the bottom side), 108 nets.

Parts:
C201, C304, C306, C307, C309, C310, C312, C314, C315, C316, C317, C318, C319, C320, C321, C323, C324, C401, C404, C405, C406: 100n; C_0402_1005Metric
C202, C403, C407, C501, C502, C503, C504, C505, C506: 100n; C_0603_1608Metric
C203, C207: 1u; C_0603_1608Metric
C204, C308: 4u7; C_0402_1005Metric
C205, C402: 10u; CP_EIA-3216-10_Kemet-I_Pad1.58x1.35mm_HandSolder
C206: 10n; C_0402_1005Metric
C208: 4u7; C_0603_1608Metric
C301, C303: 1u; C_0402_1005Metric
C302, C305: 10p; C_0402_1005Metric
C311, C313: 2u2; C_0402_1005Metric
C322: 10u; C_0805_2012Metric_Pad1.18x1.45mm_HandSolder
D201, D202, D203: D_Schottky; D_SOD-123FL
D204: BATT_LED; LED_0805_2012Metric
D205: 3V3_LED; LED_0805_2012Metric
D302, D303, D305, D306, D307: LED_WHITE; D_0603_1608Metric
D304: D_Schottky; D_SOD-323
D501, D507, D509: SFH 4550; PinHeader_1x02_P2.54mm_Vertical
D502, D503, D504, D505, D506, D508: LED; PinHeader_1x02_P2.54mm_Vertical
FB301: Optionally; L_0603_1608Metric
H201, H202, H203, H204: MountingHole; MountingHole_3mm
H401, H402, H403, H404: MountingHole; MountingHole_5mm
IC302: ESP32-S3-MINI-1-N8; ESP32S3MINI1N8
IC501: ULN2003ADR; SOIC127P600X175-16N
J201: XT30; AMASS_XT30U-M_1x02_P5.0mm_Vertical
J202: USB_C_Receptacle_USB2.0; USB_C_Receptacle_GCT_USB4105-xx-A_16P_TopMnt_Horizontal
J301: Conn_02x05_Counter_Clockwise; PinHeader_2x05_P2.54mm_Vertical
J302: Conn_01x04; PinHeader_1x04_P2.54mm_Vertical
J401, J402: Conn_01x06; PinHeader_1x06_P2.54mm_Vertical
J601: Conn_01x08; PinHeader_1x08_P2.54mm_Vertical
J602: Conn_01x05; PinHeader_1x05_P2.54mm_Vertical
JP201: Jumper_2_Bridged; PinHeader_1x02_P2.54mm_Vertical
Q201: PMOS; SOT-23-3
Q501: SFH 300 FA-3/4; PinHeader_1x02_P2.54mm_Vertical
Q502, Q503, Q504, Q505, Q506: Q_Photo_NPN; PinHeader_1x02_P2.54mm_Vertical
R201, R202: 5k1; R_0402_1005Metric
R203, R306: 10k; R_0603_1608Metric
R204: 0; R_0603_1608Metric
R205: 82k; R_0603_1608Metric
R206: 51k; R_0603_1608Metric
R207: 2k2; R_0603_1608Metric
R208: 1K; R_0603_1608Metric
R301: 1k; R_0603_1608Metric_Pad0.98x0.95mm_HandSolder
R302, R305, R309, R310, R318, R501, R503, R505, R507, R509, R511, R513, R514, R515: 1k; R_0603_1608Metric
R303: 22; R_0402_1005Metric
R304, R311, R401: 10k; R_0402_1005Metric
R307, R308: 1k; R_0402_1005Metric
R312, R313: 100; R_0603_1608Metric
R314, R315, R316, R317: 22; R_0603_1608Metric
R319: 0; R_0603_1608Metric_Pad0.98x0.95mm_HandSolder
R502, R504, R506, R508, R510, R512: 47; R_0805_2012Metric
SW201: SW_SPDT; SW_Slide_1P2T_CK_OS102011MS2Q
SW301: NRST; SW_PUSH_1P1T_6x3.5mm_H4.3_APEM_MJTP1243
SW302: SW_SPDT; SW_E-Switch_EG1271_SPDT
SW303, SW304: USER; SW_Push_1P1T_NO_6x6mm_H9.5mm
SW305: ESP_RST; SW_PUSH_1P1T_6x3.5mm_H4.3_APEM_MJTP1243
SW306: BOOT; SW_Push_1P1T_NO_6x6mm_H9.5mm
TP202, TP203, TP204, TP205, TP206, TP301: TestPoint; TestPoint_Pad_D1.0mm
U201: USBLC6-2SC6; SOT-23-6
U202: LDL1117S33R; SOT-223-3_TabPin2
U301: STM32F405RGT6; LQFP-64_10x10mm_P0.5mm
U401: TB6612FNG; SSOP-24_5.3x8.2mm_P0.65mm
Y301: 16MHz|9p|10ppm; Crystal_SMD_3225-4Pin_3.2x2.5mm

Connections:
5V_ST: D203.2 (A), J301.5, J301.6
+3.3V: C208.1, C301.1, C306.1, C308.1, C309.1, C310.1, C312.1, C314.1, C315.1, C321.1, C322.1, C323.1, C404.1, C405.1, C406.1, FB301.1, IC302.3 (3V3), J302.2 (Pin_1), J401.4 (Pin_1), J402.4 (Pin_1), J601.2, J602.1, JP201.1 (A), JP201.2 (B), Q501.1 (C), Q502.1 (C), Q503.1 (C), Q504.1 (C), Q505.1 (C), Q506.1 (C), R208.1, R311.2, R401.1, R513.2, R514.2, R515.2, SW302.3 (C), TP203.1, TP204.1, U202.2 (VO), U301.1 (VBAT), U301.19 (VDD), U301.32 (VDD), U301.48 (VDD), U301.64 (VDD), U401.20 (VCC)
+3.3VA: C303.1, C307.1, FB301.2, TP301.1, U301.13 (VDDA)
+BATT: C202.1, C203.1, C205.1, C402.1, C403.1, C407.1, D202.2 (A), D204.2 (A), Q201.2 (S), R205.2, R502.1, R504.1, R506.1, R508.1, R510.1, R512.1, TP205.1, TP206.1, U401.13 (VM2), U401.14 (VM3), U401.24 (VM1)
/Distance_sensors/Emitter1A: C504.1, D504.2 (A), R508.2
/Distance_sensors/Emitter2A: C503.1, D503.2 (A), R506.2
/Distance_sensors/Emitter3A: C502.1, D502.2 (A), R504.2
/Distance_sensors/Emitter4A: C501.1, D501.2 (A), R502.2
/Distance_sensors/Emitter5A: C505.1, D505.2 (A), R510.2
/Distance_sensors/Emitter6A: C506.1, D506.2 (A), R512.2
/Distance_sensors/Emitter_1: D504.1 (K), IC501.13 (4C)
/Distance_sensors/Emitter_2: D503.1 (K), IC501.14 (3C)
/Distance_sensors/Emitter_3: D502.1 (K), IC501.15 (2C)
/Distance_sensors/Emitter_4: D501.1 (K), IC501.16 (1C)
/Distance_sensors/Emitter_5: D505.1 (K), IC501.12 (5C)
/Distance_sensors/Emitter_6: D506.1 (K), IC501.11 (6C)
/Microcontroller/HSE OUT: C305.1, R303.2, Y301.3
/Microcontroller/OTA_RX: IC302.9 (IO5), R313.2
/Microcontroller/OTA_TX: IC302.8 (IO4), R312.2
/Microcontroller/USER_LD2_A: D302.2 (A), R302.2
/Microcontroller/USER_LD2_A_esp: D306.2 (A), R310.2
/Microcontroller/USER_LD3_A: D303.2 (A), R305.2
/Microcontroller/USER_LD3_A_esp: D307.2 (A), R318.2
/Microcontroller/USER_LD_A_esp: D305.2 (A), R309.2
/Motors/AO1: J401.6 (Pin_3), U401.1 (AO1), U401.2 (AO1)
/Motors/AO2: J401.5, U401.5 (AO2), U401.6 (AO2)
/Motors/BO1: J402.6 (Pin_3), U401.11 (BO1), U401.12 (BO1)
/Motors/BO2: J402.5, U401.7 (BO2), U401.8 (BO2)
/Power/8V_BATT: J201.2, SW201.2 (B)
/Power/DN: J202.A7 (D-), J202.B7 (D-), U201.1 (I/O1)
/Power/DP: J202.A6 (D+), J202.B6 (D+), U201.3 (I/O2)
/Power/D_PMOS: Q201.3 (D), SW201.1 (A)
/Power/LDO_VIN: C207.1, D201.1 (K), D202.1 (K), D203.1 (K), TP202.1, U202.3 (VI)
/Power/usb_vin: C204.1, D201.2 (A), R204.2
BOOT: C324.1, IC302.4 (IO0), R301.2
BatteryLEVEL: C206.1, R205.1, R206.2, U301.8 (PC0)
DRDY: J601.8 (Pin_3), U301.28 (PB2)
ESP_USB_DN: IC302.23 (IO19), U201.6 (I/O1)
ESP_USB_DP: IC302.24 (IO20), U201.4 (I/O2)
GND: C201.2, C202.2, C203.2, C204.2, C205.2, C206.2, C207.2, C208.2, C301.2, C302.2, C303.2, C304.2, C305.2, C306.2, C307.2, C308.2, C309.2, C310.2, C311.2, C312.2, C313.2, C314.2, C315.2, C316.2, C317.2, C318.1, C319.1, C320.2, C321.2, C322.2, C323.2, C324.2, C401.2, C402.2, C403.2, C404.2, C405.2, C406.2, C407.2, C501.2, C502.2, C503.2, C504.2, C505.2, C506.2, D205.1 (K), D302.1 (K), D303.1 (K), D305.1 (K), D306.1 (K), D307.1 (K), D507.1 (K), D508.1 (K), D509.1 (K), IC302.1 (GND_1), IC302.2 (GND_2), IC302.41 (IO45), IC302.42 (GND_3), IC302.43 (GND_4), IC302.46 (GND_5), IC302.47 (GND_6), IC302.48 (GND_7), IC302.49 (GND_8), IC302.50 (GND_9), IC302.51 (GND_10), IC302.52 (GND_11), IC302.53 (GND_12), IC302.54 (GND_13), IC302.55 (GND_14), IC302.56 (GND_15), IC302.57 (GND_16), IC302.58 (GND_17), IC302.59 (GND_18), IC302.60 (GND_19), IC302.61 (GND_20), IC302.62 (GND_21), IC302.63 (GND_22), IC302.64 (GND_23), IC302.65 (GND_24), IC302.66 (GND_25), IC302.67 (GND_26), IC302.68 (GND_27), IC302.69 (GND_28), IC302.70 (GND_29), IC302.71 (GND_30), IC302.72 (GND_31), IC302.73 (GND_32), IC501.8 (E), J201.1, J202.A1 (GND), J202.A12 (GND), J202.B1 (GND), J202.B12 (GND), J301.3, J301.8, J302.1 (Pin_4), J401.1 (Pin_6), J402.1 (Pin_6), J601.3 (Pin_8), J602.2 (Pin_5), R201.2, R202.2, R203.1, R206.1, R207.1, R501.1, R503.1, R505.1, R507.1, R509.1, R511.1, SW301.2 (B), SW302.1 (A), SW303.2 (B), SW304.2 (B), SW305.2 (B), SW306.2 (B), U201.2 (GND), U202.1 (GND), U301.12 (VSSA), U301.18 (VSS), U301.63 (VSS), U401.3 (PGND1), U401.4 (PGND1), U401.9 (PGND2), U401.10 (PGND2), U401.18 (GND), Y301.2, Y301.4
HSE_IN: C302.1, U301.5 (PH0), Y301.1
HSE_OUT: R303.1, U301.6 (PH1)
I2C1_SCK: J302.4 (Pin_3), J601.4, J602.4, U301.29 (PB10)
I2C1_SDA: J302.3 (Pin_2), J601.5, J602.3, U301.30 (PB11)
IMU_INT: J601.7, J602.5 (Pin_2), U301.27 (PB1)
IR_1: IC501.4 (4B), U301.39 (PC8)
IR_2: IC501.3 (3B), U301.40 (PC9)
IR_3: IC501.2 (2B), U301.41 (PA8)
IR_4: IC501.1 (1B), U301.42 (PA9)
IR_5: IC501.5 (5B), U301.23 (PA7)
IR_6: IC501.6 (6B), U301.22 (PA6)
MotorL_BIN1: U301.24 (PC4), U401.17 (BIN1)
MotorL_BIN2: U301.25 (PC5), U401.16 (BIN2)
MotorL_PWM: U301.26 (PB0), U401.15 (PWMB)
MotorR_AIN1: U301.21 (PA5), U401.21 (AIN1)
MotorR_AIN2: U301.20 (PA4), U401.22 (AIN2)
MotorR_PWM: U301.17 (PA3), U401.23 (PWMA)
NRST: D304.2 (A), R304.2, U301.7 (NRST)
unnamed: C304.1, R304.1, SW301.1 (A)
unnamed: C316.1, R307.1, SW303.1 (A)
unnamed: C319.2, R308.2, SW304.1 (A)
unnamed: D204.1 (K), R207.2
unnamed: D205.2 (A), R208.2
unnamed: D507.2 (A), R513.1
unnamed: D508.2 (A), R514.1
unnamed: D509.2 (A), R515.1
unnamed: C320.1, IC302.45 (EN), R311.1, SW305.1 (A)
unnamed: IC302.13 (IO9), R319.2
unnamed: IC302.28 (IO33), R315.2
unnamed: IC302.29 (IO34), R314.2
unnamed: IC302.31 (IO35), R317.2
unnamed: IC302.30 (IO48), R316.2
unnamed: J202.A5 (CC1), R201.1
unnamed: J202.B5 (CC2), R202.1
unnamed: Q201.1 (G), R203.2
unnamed: R301.1, SW306.1 (A)
unnamed: R306.1, SW302.2 (B)
unnamed: R306.2, U301.60 (BOOT0)
unnamed: C311.1, U301.31 (VCAP_1)
unnamed: C313.1, U301.47 (VCAP_2)
unnamed: C401.1, R401.2, U401.19 (STBY)
REC_1: Q504.2 (E), R507.2, U301.9 (PC1)
REC_2: Q503.2 (E), R505.2, U301.10 (PC2)
REC_3: Q502.2 (E), R503.2, U301.11 (PC3)
REC_4: Q501.2 (E), R501.2, U301.16 (PA2)
REC_5: Q505.2 (E), R509.2, U301.15 (PA1)
REC_6: Q506.2 (E), R511.2, U301.14 (PA0)
SPI1_CS_ESP: R315.1, U301.45 (PA12)
SPI1_MISO_ESP: R316.1, U301.56 (PB4)
SPI1_MOSI_ESP: R317.1, U301.57 (PB5)
SPI1_SCK_ESP: R314.1, U301.55 (PB3)
SWCLK: J301.10, U301.49 (PA14)
SWDIO: J301.9, U301.46 (PA13)
TIM_ENCODER_A1: J401.3 (Pin_4), U301.61 (PB8)
TIM_ENCODER_A2: J402.3 (Pin_4), U301.59 (PB7)
TIM_ENCODER_B1: J401.2, U301.62 (PB9)
TIM_ENCODER_B2: J402.2, U301.58 (PB6)
UART4_RX_OTA: R313.1, U301.52 (PC11)
UART4_TX_OTA: R312.1, U301.51 (PC10)
USER_B: C317.1, R307.2, U301.36 (PB15)
USER_B2: C318.2, R308.1, U301.37 (PC6)
USER_LD2: R302.1, U301.34 (PB13)
USER_LD2_esp: IC302.35 (IO39), R310.1
USER_LD3: R305.1, U301.35 (PB14)
USER_LD3_esp: IC302.36 (IO40), R318.1
USER_LD_esp: IC302.34 (IO38), R309.1
VBUS: C201.1, J202.A4 (VBUS), J202.A9 (VBUS), J202.B4 (VBUS), J202.B9 (VBUS), R204.1, U201.5 (VBUS)
_NRST: D304.1 (K), J301.1, R319.1

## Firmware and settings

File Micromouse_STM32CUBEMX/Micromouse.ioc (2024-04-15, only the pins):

Mcu.UserName=STM32F405RGTx
PA0-WKUP.GPIO_Label=PhotoT_6
PA0-WKUP.Signal=ADCx_IN0
PA1.GPIO_Label=PhotoT_5
PA1.Signal=ADCx_IN1
PA12.GPIO_Label=esp_spi_cs
PA12.Signal=GPIO_Output
PA13.Signal=SYS_JTMS-SWDIO
PA14.Signal=SYS_JTCK-SWCLK
PA2.GPIO_Label=PhotoT_4
PA2.Signal=ADCx_IN2
PA3.GPIO_Label=MotorR_PWM
PA3.Signal=S_TIM9_CH2
PA4.GPIO_Label=MotorR_AIN2
PA4.Signal=GPIO_Output
PA5.GPIO_Label=MotorR_AIN1
PA5.Signal=GPIO_Output
PA6.GPIO_Label=EMITTER_6
PA6.Signal=S_TIM3_CH1
PA7.GPIO_Label=EMITTER_5
PA7.Signal=S_TIM3_CH2
PA8.GPIO_Label=EMITTER_3
PA8.Signal=S_TIM1_CH1
PA9.GPIO_Label=EMITTER_4
PA9.Signal=S_TIM1_CH2
PB0.GPIO_Label=MotorL_PWM
PB0.Signal=S_TIM3_CH3
PB1.GPIO_Label=IMU_INT
PB1.Signal=GPXTI1
PB10.Signal=I2C2_SCL
PB11.Signal=I2C2_SDA
PB13.GPIO_Label=LD2
PB13.Signal=GPIO_Output
PB14.GPIO_Label=LD3
PB14.Signal=GPIO_Output
PB15.GPIO_Label=USER_BUTT1
PB15.Signal=GPXTI15
PB2.GPIO_Label=DRDY
PB2.Signal=GPXTI2
PB3.Signal=SPI1_SCK
PB4.Signal=SPI1_MISO
PB5.Signal=SPI1_MOSI
PB6.GPIO_Label=TIM_ENCODER_B1
PB6.Signal=S_TIM4_CH1
PB7.GPIO_Label=TIM_ENCODER_A1
PB7.Signal=S_TIM4_CH2
PB8.GPIO_Label=TIM_ENCODER_B2
PB8.Signal=S_TIM4_CH3
PB9.GPIO_Label=TIM_ENCODER_A2
PB9.Signal=S_TIM4_CH4
PC0.GPIO_Label=BATT_LVL
PC0.Signal=ADCx_IN10
PC1.GPIO_Label=PhotoT_1
PC1.Signal=ADCx_IN11
PC10.Signal=UART4_TX
PC11.Signal=UART4_RX
PC2.GPIO_Label=PhotoT_2
PC2.Signal=ADCx_IN12
PC3.GPIO_Label=PhotoT_3
PC3.Signal=ADCx_IN13
PC4.GPIO_Label=MotorL_BIN1
PC4.Signal=GPIO_Output
PC5.GPIO_Label=MotorL_BIN2
PC5.Signal=GPIO_Output
PC6.GPIO_Label=USER_BUTT2
PC6.Signal=GPXTI6
PC8.GPIO_Label=EMITTER_1
PC8.Signal=S_TIM8_CH3
PC9.GPIO_Label=EMITTER_2
PC9.Signal=S_TIM3_CH4
PH0-OSC_IN.Signal=RCC_OSC_IN
PH1-OSC_OUT.Signal=RCC_OSC_OUT

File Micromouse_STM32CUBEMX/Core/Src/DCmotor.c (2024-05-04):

/*
 * DCmotor.c
 *
 *  Created on: 2 maj 2024
 *      Author: Adam Iwachów
 */

#include "DCmotor.h"



void MotorDriverInit(TB6612_t *dev)
{

	dev->A01_pin  = MotorR_AIN1_Pin;
	dev->A01_port = MotorR_AIN1_GPIO_Port;

	dev->A02_pin  = MotorR_AIN2_Pin;
	dev->A02_port = MotorR_AIN2_GPIO_Port;


	dev->B01_pin  = MotorL_BIN1_Pin;
	dev->B01_port = MotorL_BIN1_GPIO_Port;

	dev->B02_pin  = MotorL_BIN2_Pin;
 	dev->B02_port = MotorL_BIN2_GPIO_Port;


	ControlMotorDirection(dev, CCW, Motor_R);

	ControlMotorSpeed(0, Motor_R);

	HAL_TIM_PWM_Start(&htim3, TIM_CHANNEL_3);
	HAL_TIM_PWM_Start(&htim9, TIM_CHANNEL_2);

}


void StopMotor(TB6612_t *dev, Motor_L_or_R Motor)
{

	if(Motor == Motor_L){
		HAL_GPIO_WritePin(dev->B01_port,dev->B01_pin , GPIO_PIN_RESET);
		HAL_GPIO_WritePin(dev->B02_port,dev->B02_pin , GPIO_PIN_RESET);
	}

	if(Motor == Motor_R){
		HAL_GPIO_WritePin(dev->A01_port,dev->A01_pin , GPIO_PIN_RESET);
		HAL_GPIO_WritePin(dev->A02_port,dev->A02_pin , GPIO_PIN_RESET);
	}

	if(Motor == BothMotors){
		HAL_GPIO_WritePin(dev->B01_port,dev->B01_pin , GPIO_PIN_RESET);
		HAL_GPIO_WritePin(dev->B02_port,dev->B02_pin , GPIO_PIN_RESET);

		HAL_GPIO_WritePin(dev->A01_port,dev->A01_pin , GPIO_PIN_RESET);
		HAL_GPIO_WritePin(dev->A02_port,dev->A02_pin , GPIO_PIN_RESET);

	}



}


void ControlMotorDirection(TB6612_t *dev, Motor_Direction Direction, Motor_L_or_R Motor)
{

if(Direction == CW){
	if(Motor == Motor_L){
			HAL_GPIO_WritePin(dev->B01_port,dev->B01_pin , GPIO_PIN_SET);
			HAL_GPIO_WritePin(dev->B02_port,dev->B02_pin , GPIO_PIN_RESET);
		}

		if(Motor == Motor_R){
			HAL_GPIO_WritePin(dev->A01_port,dev->A01_pin , GPIO_PIN_SET);
			HAL_GPIO_WritePin(dev->A02_port,dev->A02_pin , GPIO_PIN_RESET);
		}

}

else if(Direction == CCW){
	if(Motor == Motor_L){
			HAL_GPIO_WritePin(dev->B01_port,dev->B01_pin , GPIO_PIN_RESET);
			HAL_GPIO_WritePin(dev->B02_port,dev->B02_pin , GPIO_PIN_SET);
		}

		if(Motor == Motor_R){
			HAL_GPIO_WritePin(dev->A01_port,dev->A01_pin , GPIO_PIN_RESET);
			HAL_GPIO_WritePin(dev->A02_port,dev->A02_pin , GPIO_PIN_SET);
		}

	}
}



void ControlMotorSpeed(uint16_t speed, Motor_L_or_R Motor)
{

	if(speed > 100){
		speed = 99;
	}

	if(Motor == Motor_R){
		__HAL_TIM_SetCompare(&htim9, TIM_CHANNEL_2, speed);
	}

	else if(Motor == Motor_L){
		__HAL_TIM_SetCompare(&htim3, TIM_CHANNEL_3, speed);
	}

	else if(Motor == BothMotors){
		__HAL_TIM_SetCompare(&htim3, TIM_CHANNEL_3, speed);
		__HAL_TIM_SetCompare(&htim9, TIM_CHANNEL_2, speed);
	}


}

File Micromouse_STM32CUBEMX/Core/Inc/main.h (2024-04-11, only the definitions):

#define BATT_LVL_Pin GPIO_PIN_0
#define BATT_LVL_GPIO_Port GPIOC
#define PhotoT_1_Pin GPIO_PIN_1
#define PhotoT_1_GPIO_Port GPIOC
#define PhotoT_2_Pin GPIO_PIN_2
#define PhotoT_2_GPIO_Port GPIOC
#define PhotoT_3_Pin GPIO_PIN_3
#define PhotoT_3_GPIO_Port GPIOC
#define PhotoT_6_Pin GPIO_PIN_0
#define PhotoT_6_GPIO_Port GPIOA
#define PhotoT_5_Pin GPIO_PIN_1
#define PhotoT_5_GPIO_Port GPIOA
#define PhotoT_4_Pin GPIO_PIN_2
#define PhotoT_4_GPIO_Port GPIOA
#define MotorR_PWM_Pin GPIO_PIN_3
#define MotorR_PWM_GPIO_Port GPIOA
#define MotorR_AIN2_Pin GPIO_PIN_4
#define MotorR_AIN2_GPIO_Port GPIOA
#define MotorR_AIN1_Pin GPIO_PIN_5
#define MotorR_AIN1_GPIO_Port GPIOA
#define EMITTER_6_Pin GPIO_PIN_6
#define EMITTER_6_GPIO_Port GPIOA
#define EMITTER_5_Pin GPIO_PIN_7
#define EMITTER_5_GPIO_Port GPIOA
#define MotorL_BIN1_Pin GPIO_PIN_4
#define MotorL_BIN1_GPIO_Port GPIOC
#define MotorL_BIN2_Pin GPIO_PIN_5
#define MotorL_BIN2_GPIO_Port GPIOC
#define MotorL_PWM_Pin GPIO_PIN_0
#define MotorL_PWM_GPIO_Port GPIOB
#define IMU_INT_Pin GPIO_PIN_1
#define IMU_INT_GPIO_Port GPIOB
#define DRDY_Pin GPIO_PIN_2
#define DRDY_GPIO_Port GPIOB
#define LD2_Pin GPIO_PIN_13
#define LD2_GPIO_Port GPIOB
#define LD3_Pin GPIO_PIN_14
#define LD3_GPIO_Port GPIOB
#define USER_BUTT1_Pin GPIO_PIN_15
#define USER_BUTT1_GPIO_Port GPIOB
#define USER_BUTT2_Pin GPIO_PIN_6
#define USER_BUTT2_GPIO_Port GPIOC
#define EMITTER_1_Pin GPIO_PIN_8
#define EMITTER_1_GPIO_Port GPIOC
#define EMITTER_2_Pin GPIO_PIN_9
#define EMITTER_2_GPIO_Port GPIOC
#define EMITTER_3_Pin GPIO_PIN_8
#define EMITTER_3_GPIO_Port GPIOA
#define EMITTER_4_Pin GPIO_PIN_9
#define EMITTER_4_GPIO_Port GPIOA
#define esp_spi_cs_Pin GPIO_PIN_12
#define esp_spi_cs_GPIO_Port GPIOA
#define TIM_ENCODER_B1_Pin GPIO_PIN_6
#define TIM_ENCODER_B1_GPIO_Port GPIOB
#define TIM_ENCODER_A1_Pin GPIO_PIN_7
#define TIM_ENCODER_A1_GPIO_Port GPIOB
#define TIM_ENCODER_B2_Pin GPIO_PIN_8
#define TIM_ENCODER_B2_GPIO_Port GPIOB
#define TIM_ENCODER_A2_Pin GPIO_PIN_9
#define TIM_ENCODER_A2_GPIO_Port GPIOB

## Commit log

2024-03-07 cos tam cos tam
    [DistanceSensors&IMU.kicad_sch]
2024-03-07 DC driver
    [Motors.kicad_sch]
2024-03-07 trzeba dobrać bucka
    [Power.kicad_sch]
2024-03-07 dodaję adaptery i ich footprinty
    [adapter_ESP32-B_Cu.gbr, adapter_ESP32-B_Mask.gbr, adapter_ESP32-B_Paste.gbr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]
2024-03-07 Prawie skończone
    [DistanceSensors.kicad_sch, Microcontroller.kicad_sch, Micromouse.kicad_sch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]
2024-03-08 druga wersja płytki stm32 do recenzji
    [adapter_STM32-B_Cu.gbr, adapter_STM32-B_Mask.gbr, adapter_STM32-B_Paste.gbr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]
2024-03-08 zapomniałem kilku ścieżek, teraz jest całość
    [adapter_STM32-B_Cu.gbr, adapter_STM32-B_Mask.gbr, adapter_STM32-B_Paste.gbr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]
2024-03-09 Dodaje wszystko nie chce mi sie z tym bawic
    [DistanceSensors.kicad_sch, Microcontroller.kicad_sch, Micromouse.kicad_sch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]
2024-03-11 wstępnie zrobiony adapter ESP32-S3. oceń czy jest git to zrobię footprinta do niego
    [Microcontroller.kicad_sch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]
2024-03-11 drobne zmiany
    [DistanceSensors.kicad_sch, Microcontroller.kicad_sch, Micromouse.kicad_pcb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]
2024-03-14 poprawione esp32s3
    [adapter_ESP32-S3.kicad_pcb]
2024-03-14 folder footprintów
2024-03-28 Final version
    [DistanceSensors.kicad_sch, Microcontroller.kicad_sch, Micromouse.kicad_pcb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]
2024-04-12 improving the hierarchical scheme
    [Micromouse.kicad_sch]
2024-04-12 changing engines
    [Motors.kicad_sch]
2024-04-16 Full schematics in pdf file
2024-05-04 DC motors driver

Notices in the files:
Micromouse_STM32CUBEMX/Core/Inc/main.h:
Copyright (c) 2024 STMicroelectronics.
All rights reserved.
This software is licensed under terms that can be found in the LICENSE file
